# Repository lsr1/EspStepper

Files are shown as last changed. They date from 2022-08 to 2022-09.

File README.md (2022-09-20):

# EspStepper

control a [NEMA stepper motor](https://en.wikipedia.org/wiki/Stepper_motor#NEMA_stepper_motors) with [Home Assistant](https://www.home-assistant.io/) using a D1 mini via [ESPHome](https://esphome.io/). 

## Executive Summary
* This project provides a solution for controlling a NEMA stepper motor with Home Assistant (via ESPHome), utilizing a D1 mini board.
* This project consists of a KiCad project that gives you the [Gerber files](gerber/gerber.zip) to order a PCB (e.g. at [JLCPCB](https://cart.jlcpcb.com) onto which (mostly) passive components (pinheaders/sockets) are soldered. Then you plug on some standard modules you can get from [AliExpress](https://www.aliexpress.com), create a device in Home Assistant and are pretty much done.
* For the impatient: Go to [Installation](#Installation).

## Picture
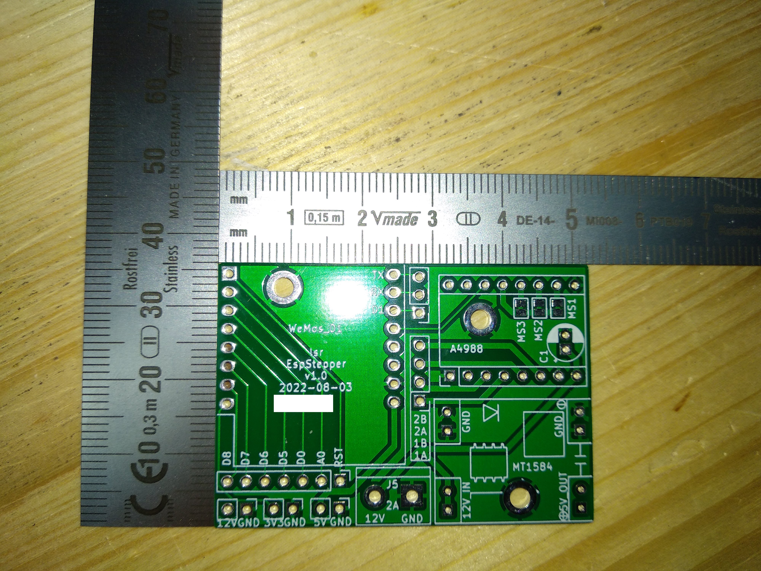
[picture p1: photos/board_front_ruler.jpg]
pcb image


## Sidenotes
This is my second "public GitHub" project (see here my [first one](https://github.com/lsr1/wb2s-to-esp12)). I made something (crude) that I nevertheless think might be useful for somebody else. That is also the reason why this readme will be very long - for myself I want to document the story behind it for my records, and (hopefully) for your pleasure :-) </br>
Despite the verbosity of the README, it assumes that you know how to solder, how to work with a multi meter and your way around Home Assistant and ESPHome. Some things here are weirdly specific, while some are infuriatingly generic (assuming a lot of knowhow).

## Preamble (Why)
* I did this because I wanted an easy way to drive a stepper via Home Assistant. I couldn't find an idiot-proof end2end solution on the whole internet - everything was just pieces. There was just no "easy" way with   all the parts connected (be it SW or HW). So I made <i>this</i>.
* I did this to scratch an itch of mine, and to hone my skills in all the tools along the toolchain. For me, this was really interdisciplinary. 

## Design Decisions (and other reasoning)
### Goals
* Drive exactly one NEMA stepper.
* Have only one input voltage that works for the stepper but also powers the rest of the board. 
* Have mainly only passive components on the PCB to make it easy to solder.
* Use as many widely available off-the-shelf components and modules as possible over working directly with parts/MCUs.
* Have a compact PCB design.
* Don't use jumpers for MS1/2/3 but solder-bridges (uses less space).
* There are already 3 voltages on the board - make them available.
* Enable usage of unused D1 mini pins via pinheaders.
* Have enough GND pins. 
* Have short high-voltage tracks.
* Have everything socketed. 
* Have the antenna of the D1 board protrude over the PCB to avoid interference from PCB copper fill (I didn't want to create a keep-out zone; not for a specific reason - I just wanted to make due w/o one). 
* The silkscreen on the board shall be self-speaking for modules over the usual 'short nomenclature' (e.g. "J1"). 
* C1 for stabilizing voltage when the NEMA stepper turns on should be optional. 
* No SMD components (to make it easier to solder for novices).
* Voltage pins are intentionally not on one continuous pin row but 3x2.
* Low cost.

### Non-goals
* No need for perfectly aligned mounting holes.
* No need for silent steppers (thus use A4988). 
* Micro-USB port of the D1 does not need to be available when socketed.
* No need for energy efficiency. 
* No need for "perfect" PCB/circuit design (<i>done is better than perfect</i>).

## BOM (for 1 module)
* 1 x PCB (see [Installation](#Installation))
* 1 x D1 Mini (with normal pinheaders looking 'down'; from Ali)
* 1 x A4988 stepper driver (from Ali)
* 1 x MP1584 DC-DC step-down Module with LM2596 (from Ali)
* 1 x KF301- 2Pin 5.0mm screw-terminal (from Ali)
* 4 x 1x8pin female pinheaders 2.54 mm (from Ali)
* 4 x 1x2pin female pinheaders 2.54 mm (from Ali)
* standard 1 row 2.54mm male pinheaders
* (optional) 1 x capacitor (>= 12V, THT radial D5.0mm / P2.00mm)

## Installation
This will be long. Brace.

### Order PCBs
* Go to [JLCPCB](https://cart.jlcpcb.com/quote) and upload the [gerber.zip](gerber/gerber.zip). Sidenote: I'm neither sponsored nor do I endorse them specifically, I just find them convenient. Make sure you select the correct PCB thickness (1.2 mm). I also set "Remove Order Number" to "Specify a location" (layout contains a field for this). No other special settings.

### Soldering
* Solder the components. No special advice here - it should be pretty straight forward.
* Close the MS1/2/3 solder bridges for microstepping.
* If you populate the C1 capacitor, make sure you leave enough 'height' of the legs to fold it down 90 degrees to lie flat (otherwise the A4988 won't fit above).

### Tuning
* <b>BEFORE</b> putting on all modules and connect power, tune the MP1584 to 5V output. Do this <b>now</b>.
* The A4988 needs to be tuned to output the correct voltage for your NEMA stepper. I will not document here how to do this - please google it. 

### Assemply
* Put all modules on the board. Take care of the orientation - there is absolutely no safeguard against voltage reversal or such things.
* Usually an A4988 stepper comes with a mini-heatsink. Put it on.
* Provide 12V input (VCC is left on the screw terminal, GND is right).
* If your NEMA stepper cable is connected [like this](photos/NEMA_cabling.png), then the pins go on the board like shown in the table below (however: don't trust this - your stepper might be different, your cable might be different, etc.):

|row #|color|board pin|
---| --- | ---
1|BLK|2B
2|BLU|2A
3|GRN|1B
4|RED|1A

### Software
* It is assumed you have a working instance of Home Assistant with a working ESPHome plugin. If not, please google how to get there.
* Create an ESPHome device in Home Assistant with the configuration as basis noted in [this file](HomeAssistant/my-stepper.yaml). Modify to your gusto.
* Create an automation in Home Assistant with the configuration noted in [this file](HomeAssistant/automation.yaml). Modify to your gusto. Note: The automation includes a slider control that is not documented here. For POC, just run the automation manually.
* If you run the automation (manually), your stepper should turn.
* Read up on the parameters and play around with them - I am intentionally not providing more info or limits or the like. 

### Caveats / FAQ
* This is not the work of a professional, and thus has not been load/fuzzy/destructive-tested. All things could happen, thus this project comes without any warranty. Never use it anywhere in a production situation.

* You can't solder the MP1584 directly on the board even if you don't care about the mouting-hole: The holes for the pins are too small (only the female pin-headers fit, but no the male pinheaders directly). This might be changed on a v2 of the board.

* Todo for v2: Mark the GND pin for the A4988 with silkscreen on the PCB to make it easier to plug in.

* Todo for v2: Mark the diameter of the mounting holes with silkscreen on the PCB. Saves reaching for the caliper.

* Before publishing I got feedback from some dear friends to put ferrit-pearls in series to the 5V for the A4988 and the D1 to make sure the voltage is "clean". I consciously omitted that feedback for simplicity reasons.

* The mounting holes are connected to GND because ... no reason. 

* There is intentionally no ESPHome binary provided for download and flashing here.

* I'm neither affiliated with nor do I get money from JLC nor Ali, I just find both convenient. 

* Why is there no YT video describing this whole thing? - B/c IMHO YT sucks for technical documentation. 

* The KiCad project does not have all components/footprints - I got them from various online sources and didn't track the copyright - sorry.
* I would love to have some useful web GUI in the ESPHome code - but I don't know how to do that. 

## License and Legalese
* May be (re)used for personal/private use only and not sold/licensed for commercial or financial gain. This non-standard license should make it impossible and really difficult for commercial enterprises to profit from my work (pay people to design this!), but enable the hobbyist/enthusiast to work with it.
* If I have inadverently (re-)used your work without either properly attributing it or something, please let me know - I'd be happy to correct this.

## Donations
Yes please.

## Feedback
Also yes please! (I hope I figure out how this whole pull-request thing works...)

## Shoutout ...
* ... to [CCC](https://www.ccc.de) and [CCCZH](https://www.ccczh.ch/)!
* ... to all FOSS contributors that helped making SW that enabled me to do this. Nanos gigantium humeris insidentes.

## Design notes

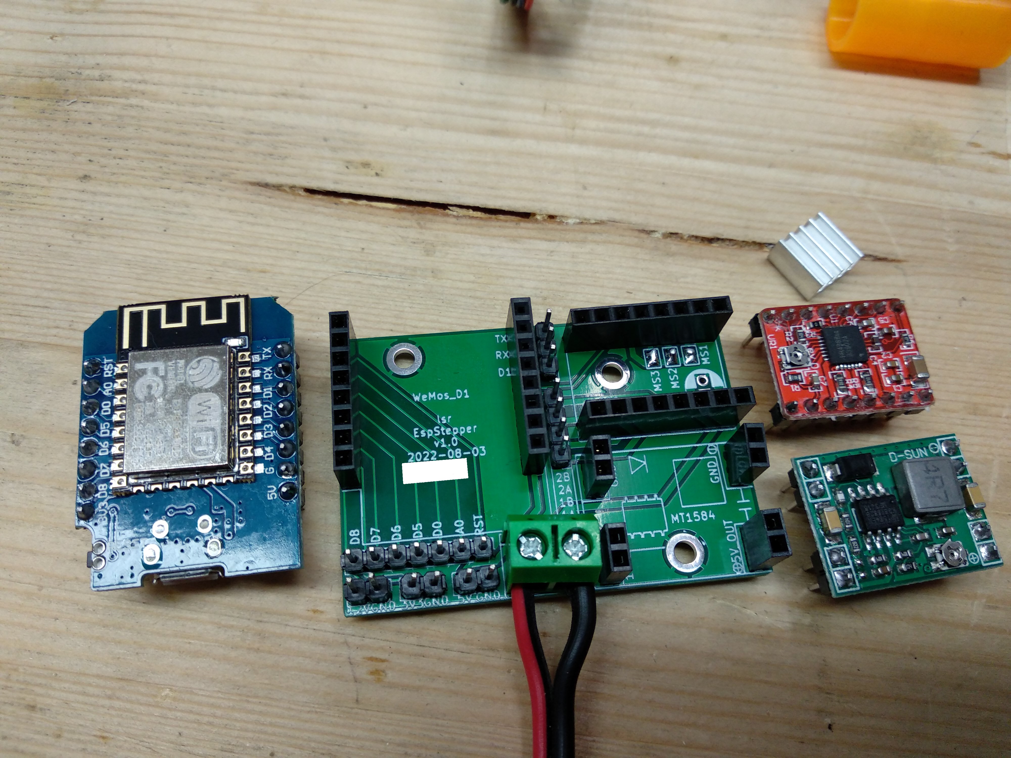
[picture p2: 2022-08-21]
photos/board_with_modules.jpg

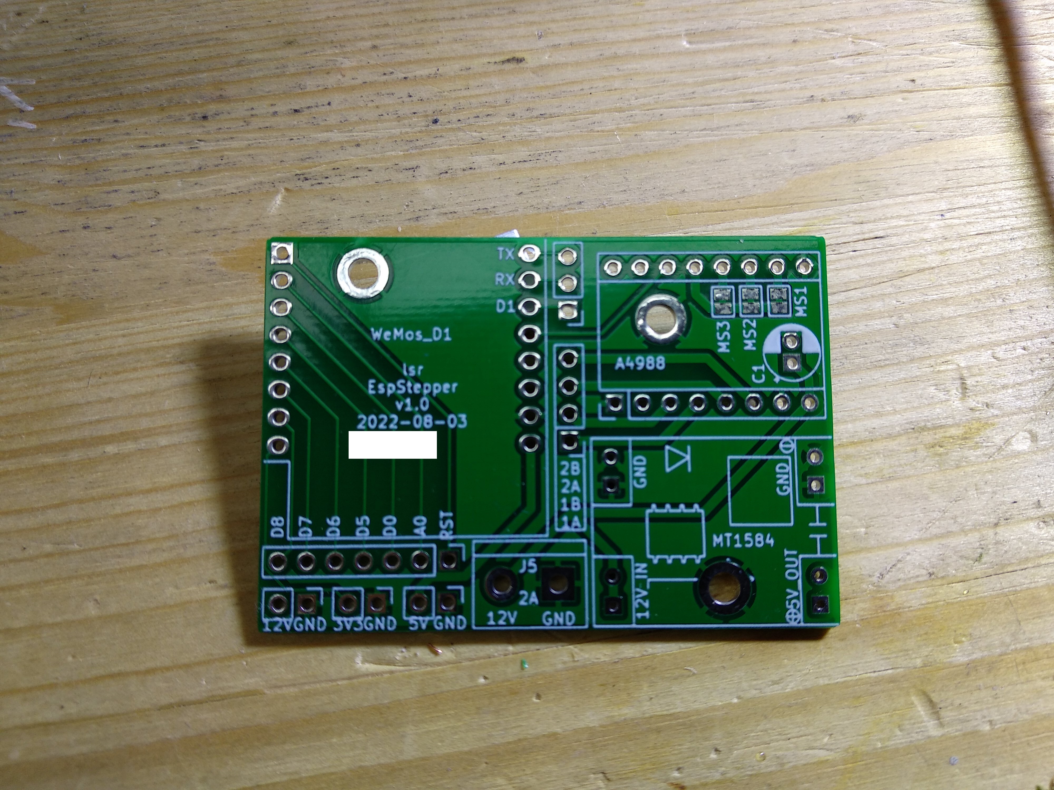
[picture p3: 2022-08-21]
photos/board_front.jpg

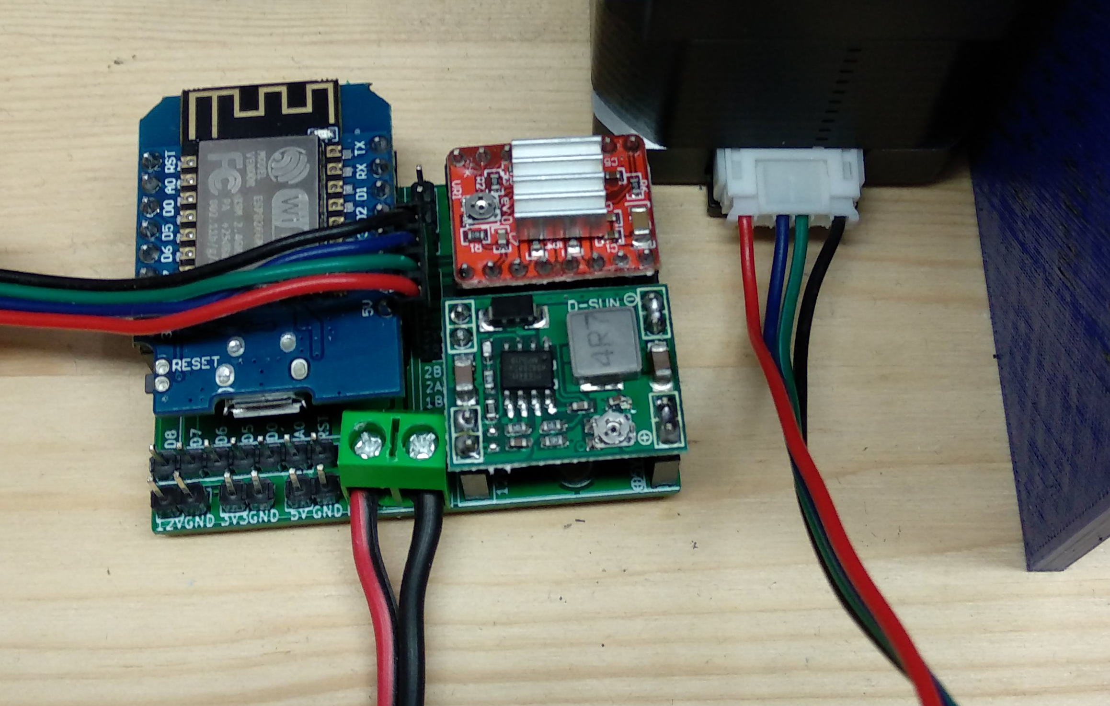
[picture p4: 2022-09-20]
photos/NEMA_cabling.png

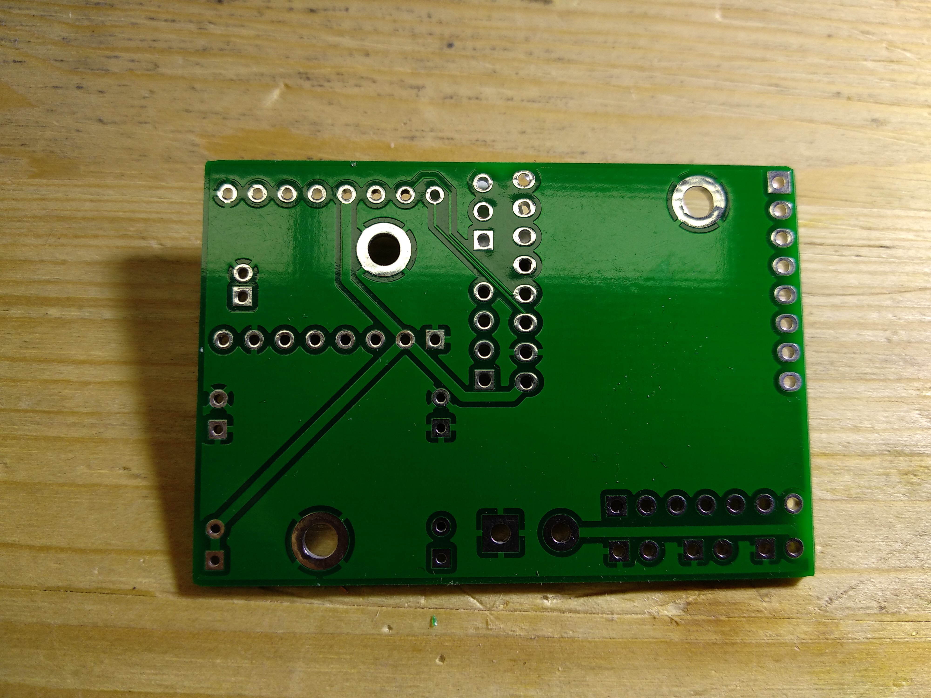
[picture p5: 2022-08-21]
photos/board_back.jpg

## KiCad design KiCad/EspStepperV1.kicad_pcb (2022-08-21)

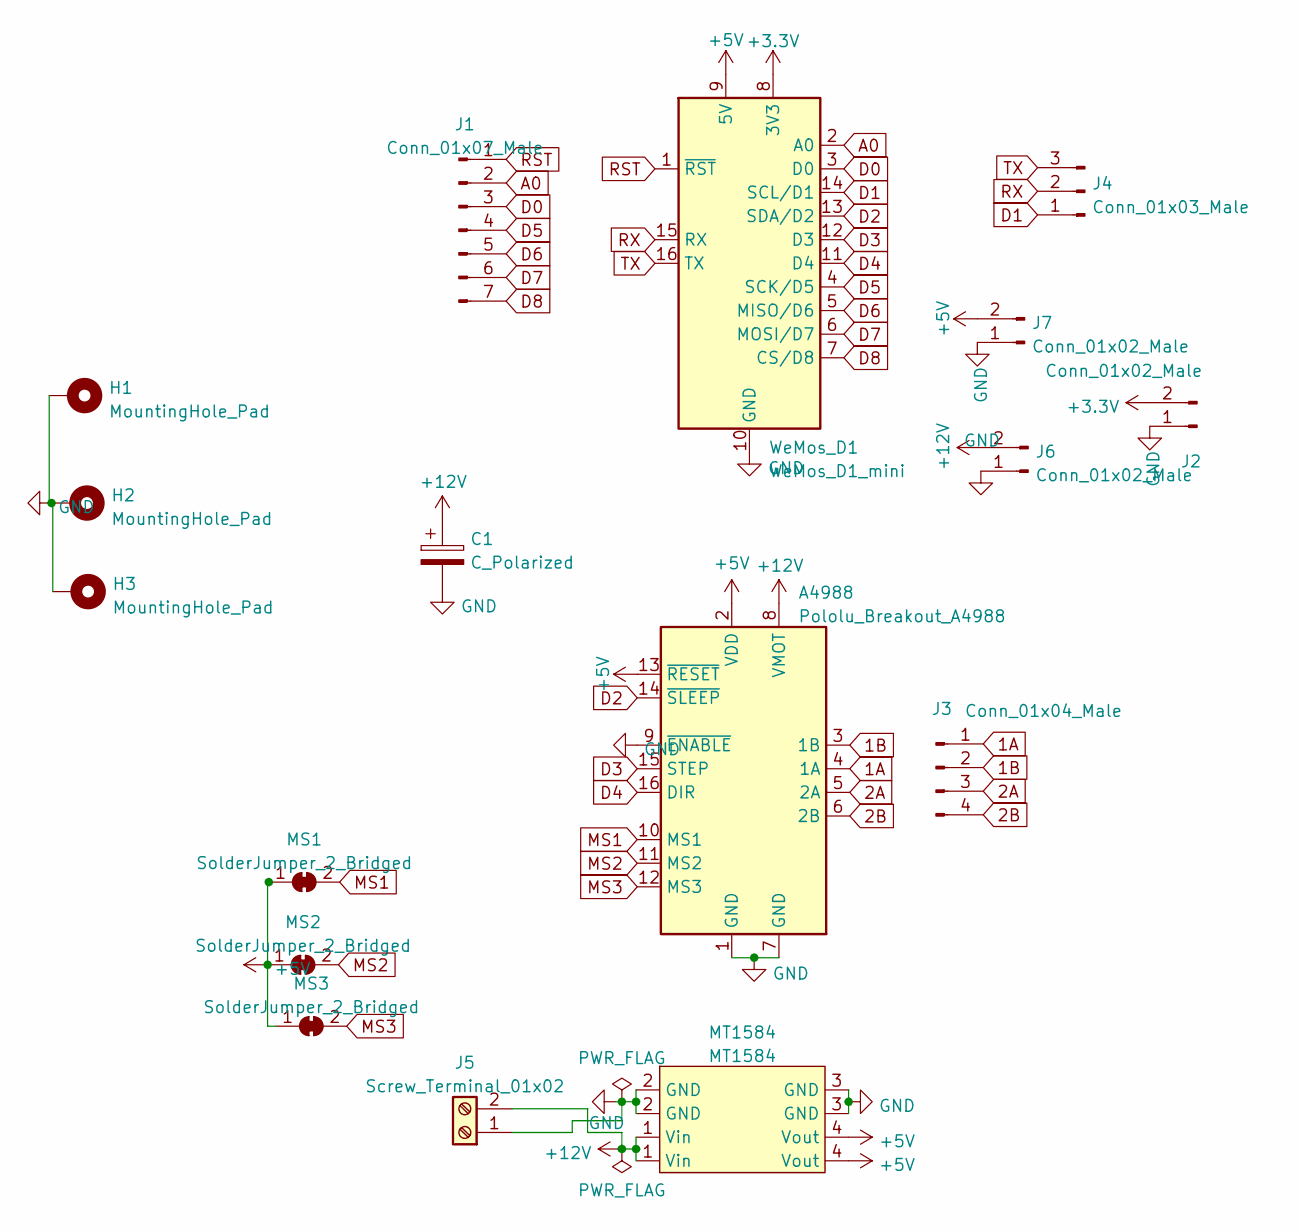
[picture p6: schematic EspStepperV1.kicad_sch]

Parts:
A4988: Pololu_Breakout_A4988; Pololu_Breakout-16_15.2x20.3mm
C1: C_Polarized; CP_Radial_D5.0mm_P2.00mm
H1, H2, H3: MountingHole_Pad; MountingHole_2.7mm_M2.5_DIN965_Pad_TopBottom
J1: Conn_01x07_Male; PinHeader_1x07_P2.54mm_Vertical
J2, J6, J7: Conn_01x02_Male; PinHeader_1x02_P2.54mm_Vertical
J3: Conn_01x04_Male; PinHeader_1x04_P2.54mm_Vertical
J4: Conn_01x03_Male; PinHeader_1x03_P2.54mm_Vertical
J5: Screw_Terminal_01x02; TerminalBlock_bornier-2_P5.08mm
MS1, MS2, MS3: SolderJumper_2_Bridged; SolderJumper-2_P1.3mm_Bridged_Pad1.0x1.5mm
MT1584: MT1584; MP1584_buck_module
WeMos_D1: WeMos_D1_mini; WEMOS_D1_mini_light

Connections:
1A: A4988.4 (1A), J3.1
1B: A4988.3 (1B), J3.2
2A: A4988.5 (2A), J3.3
2B: A4988.6 (2B), J3.4
+3V3: J2.2, WeMos_D1.8 (3V3)
+5V: A4988.2 (VDD), A4988.13 (~RESET), J7.2, MS1.1 (A), MS2.1 (A), MS3.1 (A), MT1584.4 (Vout), WeMos_D1.9 (5V)
A0: J1.2, WeMos_D1.2 (A0)
D0: J1.3, WeMos_D1.3 (D0)
D1: J4.1, WeMos_D1.14 (SCL/D1)
D2: A4988.14 (~SLEEP), WeMos_D1.13 (SDA/D2)
D3: A4988.15 (STEP), WeMos_D1.12 (D3)
D4: A4988.16 (DIR), WeMos_D1.11 (D4)
D5: J1.4, WeMos_D1.4 (SCK/D5)
D6: J1.5, WeMos_D1.5 (MISO/D6)
D7: J1.6, WeMos_D1.6 (MOSI/D7)
D8: J1.7, WeMos_D1.7 (CS/D8)
MS1: A4988.10 (MS1), MS1.2 (B)
MS2: A4988.11 (MS2), MS2.2 (B)
MS3: A4988.12 (MS3), MS3.2 (B)
RST: J1.1, WeMos_D1.1 (~RST)
RX: J4.2, WeMos_D1.15 (RX)
TX: J4.3, WeMos_D1.16 (TX)

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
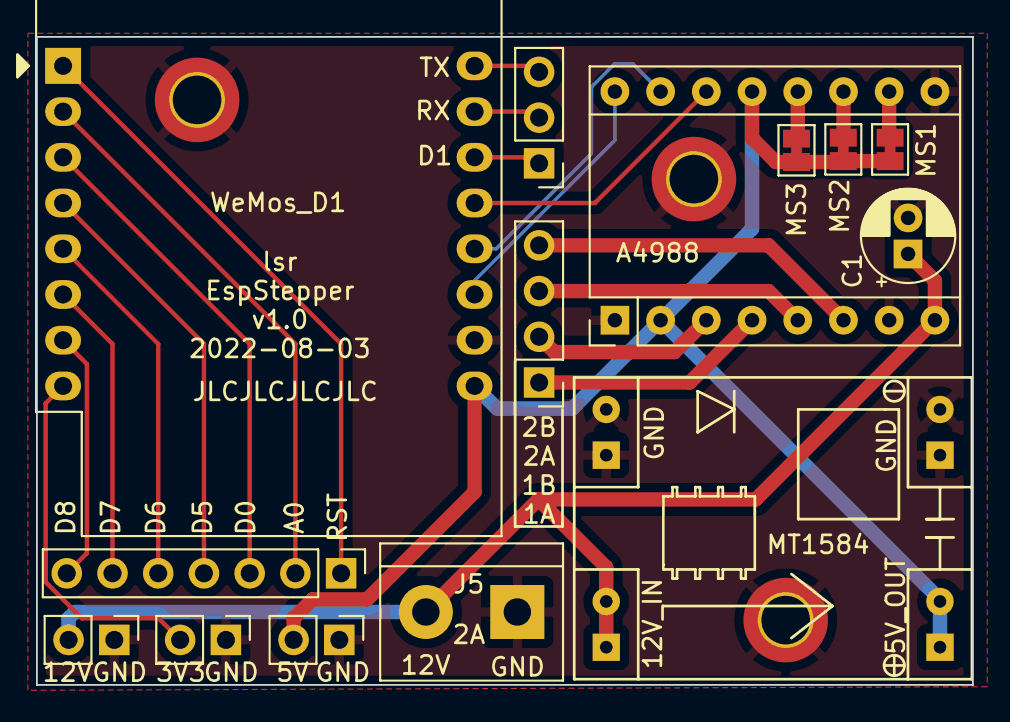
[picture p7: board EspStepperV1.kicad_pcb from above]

Board: 2 copper layers, 52.0 x 36.0 mm, 17 parts (0 on the bottom side), 24 nets.
